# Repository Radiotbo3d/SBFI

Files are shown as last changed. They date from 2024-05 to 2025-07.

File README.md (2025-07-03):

# SBFI (Smooth Beefy Front Idlers)

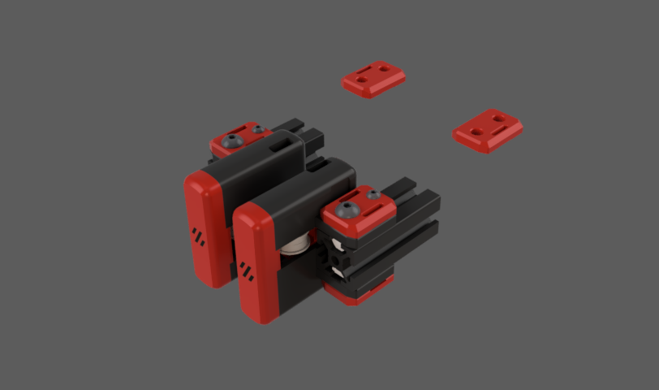
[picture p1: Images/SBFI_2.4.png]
SBFI family render

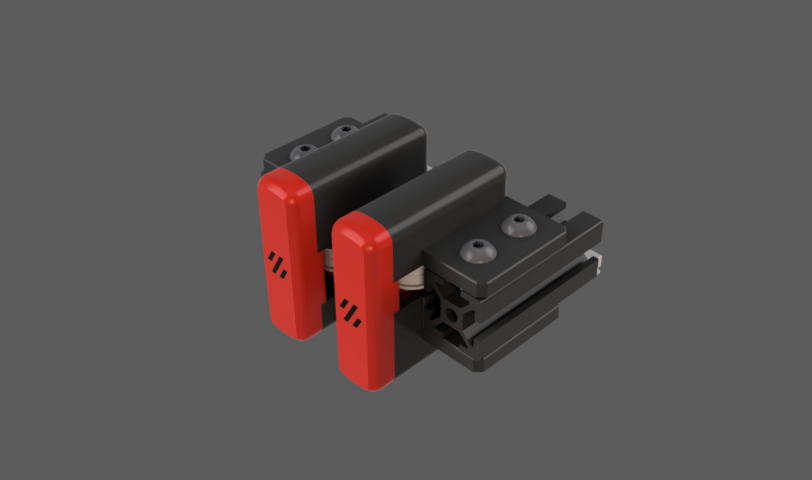
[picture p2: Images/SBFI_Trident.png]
SBFI family render


### What is this?

These are replacement front idlers for Vorons (and Voron-based machines).
This design is available for Voron Trident and Voron 2.4.

### Improvements?

This is a version remixed/based on [BFI](https://github.com/clee/VoronBFI/tree/main)
my version has several improvements or things that I have changed to fit my needs.
#### Changes:
- They are now symetrical
- They now have a magnetic cover so you don't need to see those screws anymore
- They now have curved edges instead of chamfers (very similar to [Ramalama2](https://github.com/Ramalama2/Voron-2-Mods/tree/main/Front_Idlers))

### Some more things you need to know:
You can also find this model on:
- [Clee's usermods github](https://github.com/clee/VoronBFI/tree/main/usermods#other-bfi-forksvariants)
- [Printables](https://www.printables.com/model/890840-sbfi-smooth-beefy-front-idlers)

All the clips for the z belts on the voron 2.4 are the exact same as the BFI

The internal bearing stack holder is also the exact same as the BFI (so if you had the BFI and you want to change to SBFI you don't need to reprint that part)

The front magnetic covers can be printed with MMU/AMS or you can print them as separate gcodes without removing the build plate after each print, or you can just print them with the negative of the voron logo (single color)

## BOM

### SBFI for Voron 2.4
(It's the exact same BOM as BFI but you also need 8 6x3mm magnets (4 per idler) "it will also work fine with 4 magnets (2 per idler) but I still recomend you use 8 magnets"

For V2.4, you'll need:
- 4× M5×30 BHCS 
- 4× M5 hex nuts
- 2× 5mm-diameter pin, 18mm long
- 2× M3 t-nuts
- 2× M3×16 BHCS

...plus the same shim/bearing stack setup for each idler as the original stock front idlers.

### SBFI for Trident
(It's the exact same BOM as BFI but you also need 8 6x3mm magnets (4 per idler) "it will also work fine with 4 magnets (2 per idler) but I still recomend you use 8 magnets" (and the exception that you need to change the M5x40 SHCS for M5x40 BHCS)

For Trident, you'll need:
- 4× M5×40 BHCS
- 4× M5 hex nuts
- 2× 5mm-diameter pin, 18mm long

...plus the same shim/bearing stack setup for each idler as the original stock front idlers.

## Belt / Idler Skew Tuning

BFI has a tendency to wear down belts, a known issue that occurs when the idlers are misaligned. This is also discussed in an upstream issue: https://github.com/clee/VoronBFI/issues/29.

You can use the macro below to move the tool head in a circular pattern within its range of motion. This ensures the belts keep moving consistently while you adjust the idlers.

```
[gcode_macro _TEST_BELTS]
gcode:
  {% if 'x' not in printer.toolhead.homed_axes %}
  {% if 'y' not in printer.toolhead.homed_axes %}
  G28 X Y 
  {% endif %}
  {% endif %}
 
  {% set circles = params.S|default(1)|int %}
  {% set rate = params.F|default(18000)|int %}
  {% for i in range(circles) %}
      G1 X{printer.toolhead.axis_minimum.x + 15} Y{printer.toolhead.axis_minimum.y + 15}  F{rate}
      G1 X{printer.toolhead.axis_maximum.x - 15} Y{printer.toolhead.axis_minimum.y + 15}  F{rate}
      G1 X{printer.toolhead.axis_maximum.x - 15} Y{printer.toolhead.axis_maximum.y - 15} F{rate}
      G1 X{printer.toolhead.axis_minimum.x + 15} Y{printer.toolhead.axis_maximum.y - 15}  F{rate}
      G1 X{printer.toolhead.axis_minimum.x + 15} Y{printer.toolhead.axis_minimum.y + 15}  F{rate}
    {% endfor %}
    G1 X{ printer.toolhead.axis_maximum.x / 2  } Y{printer.toolhead.axis_maximum.y  /2}  F{rate}
```

Call this macro with the parameter S to set the number of circles. For example, use `_TEST_BELTS S=20` to run 20 circles.

As the belts move, you can better observe if they are riding up on the flanges. To adjust, loosen the side you want the belt to shift toward—if it's riding up on the top flange, loosen the top bolt; if it's on the bottom flange, loosen the bottom bolt.
<br/>
<br/>
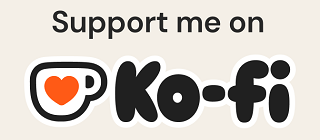
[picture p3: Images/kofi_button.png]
support me (https://ko-fi.com/radiotbo)

<br/>
## You can also support me by liking or downloading the files trough [printables](https://www.printables.com/model/890840-sbfi-smooth-beefy-front-idlers)
<br/>
# Contributors
I want to thank everyone who has helped to develop this project.

- [@clee](https://github.com/clee) (Original BFI)
- [@Ramalama2](https://github.com/Ramalama2) (Curved edges design)
- [@Shaly](https://github.com/Apstarkdev) (Improvement suggestions and testing)
- [@TheVoronModder](https://www.youtube.com/@TheVoronModder) (Improvement suggestions) (check out his [Chunky Alpaca Idlers](https://www.printables.com/model/678823-voron-24-trident-chunky-alpaca-tensioners))
- @Micky (Curved edges suggestion)
- [@Vajonam](https://github.com/vajonam) (Feedback and Macro Development)

And If someone has any suggestion for improving the design or maybe some cool features I could add, please don't hesitate to tell me.

You can either contact me through Github or through Discord "radiotbo" (I'd probably answer you faster through discord)

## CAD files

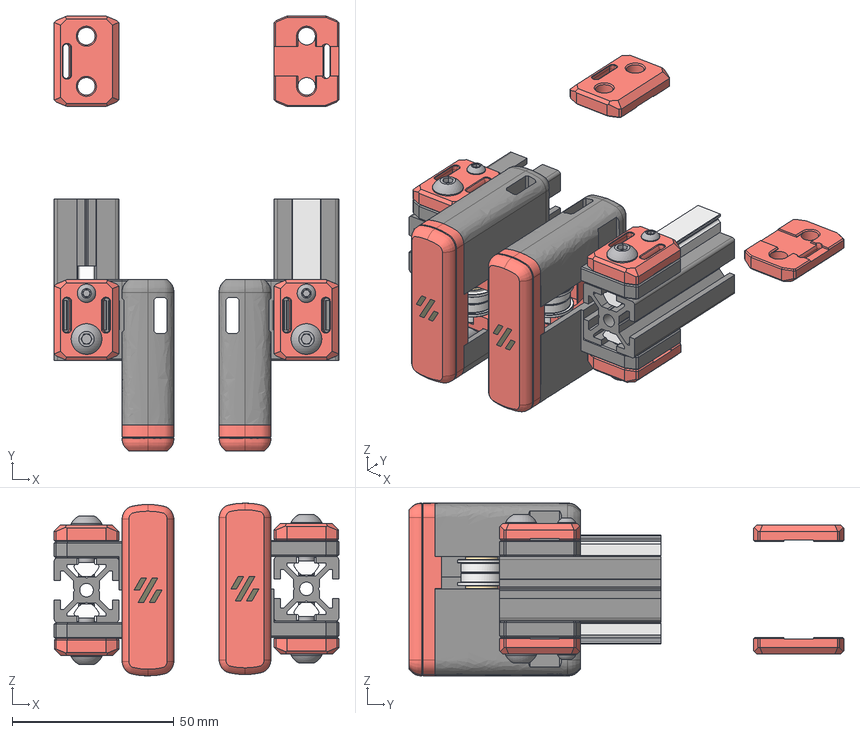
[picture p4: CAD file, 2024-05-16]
CAD/Voron_2.4/SBFI_Voron_2.4.step
88.1 x 134.5 x 53.4 mm
Printable_Parts x 2
Gantry x 2
Fasteners x 2

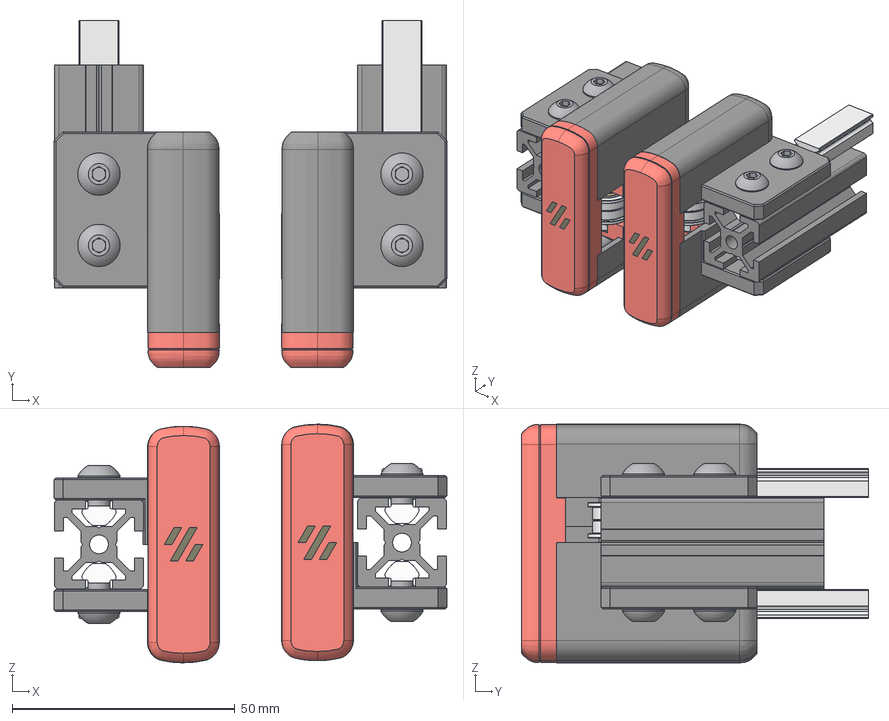
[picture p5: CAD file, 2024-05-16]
CAD/Voron_Trident/SBFI_Voron_Trident.step
88.2 x 77.9 x 53.6 mm
Printable_Parts x 2
Gantry x 2
Fasteners x 2

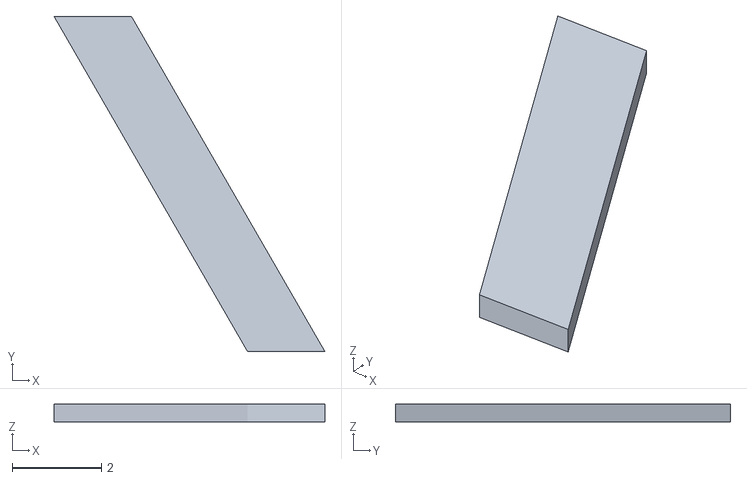
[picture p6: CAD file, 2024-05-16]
STLs/Voron_2.4/SBFI-V2.4_Voron_Logo2_x2.stl
6.06 x 7.50 x 0.4

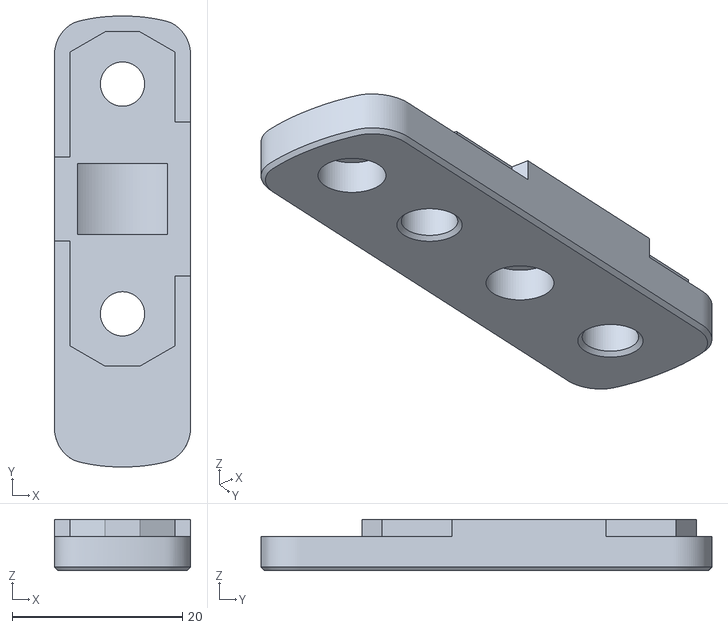
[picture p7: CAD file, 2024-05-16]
STLs/Voron_2.4/[a]_SBFI-V2.4_Middle_x2.stl
16.0 x 53.0 x 6.00

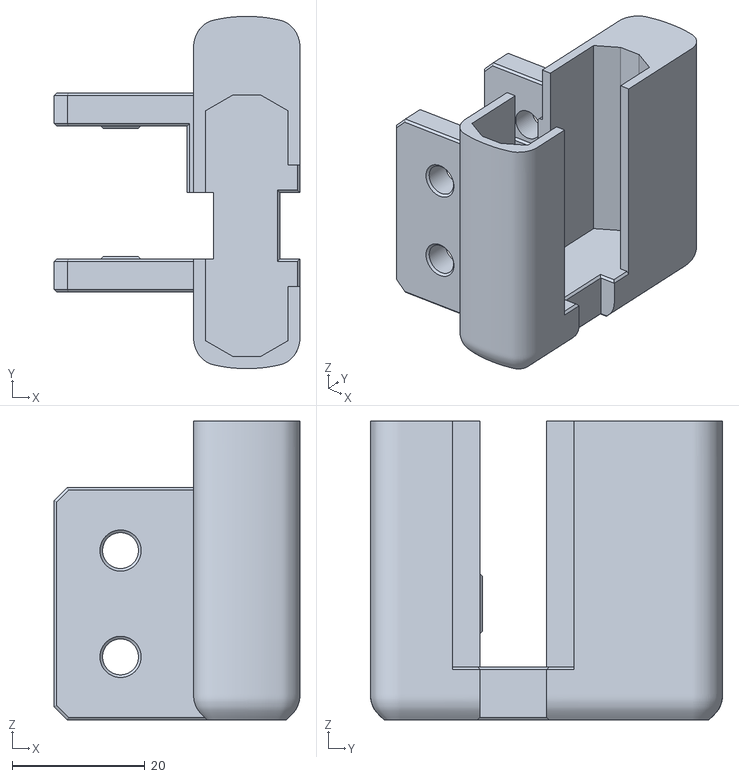
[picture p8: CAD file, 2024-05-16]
STLs/Voron_Trident/SBFI-VT_Housing_x2.stl
37.0 x 53.0 x 45.0

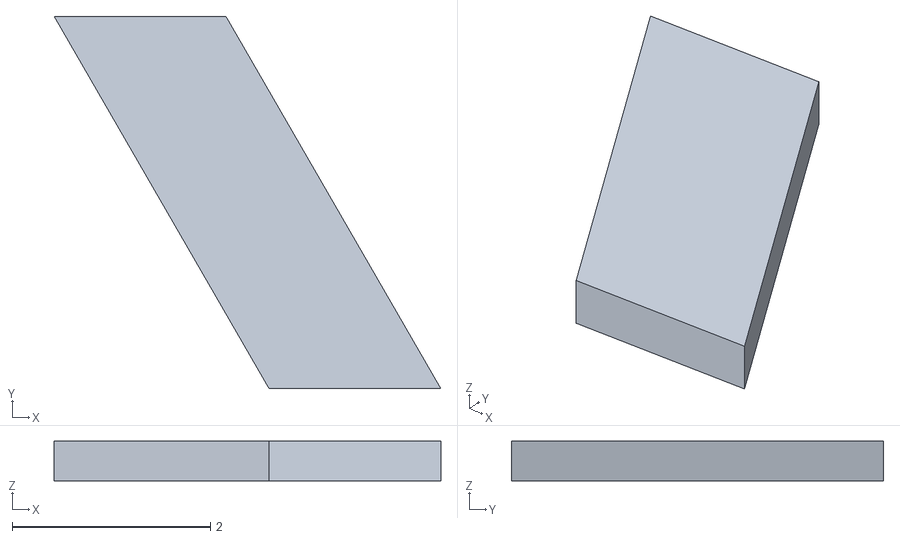
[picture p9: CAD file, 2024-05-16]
STLs/Voron_2.4/SBFI-V2.4_Voron_Logo1_x2.stl
3.90 x 3.75 x 0.4

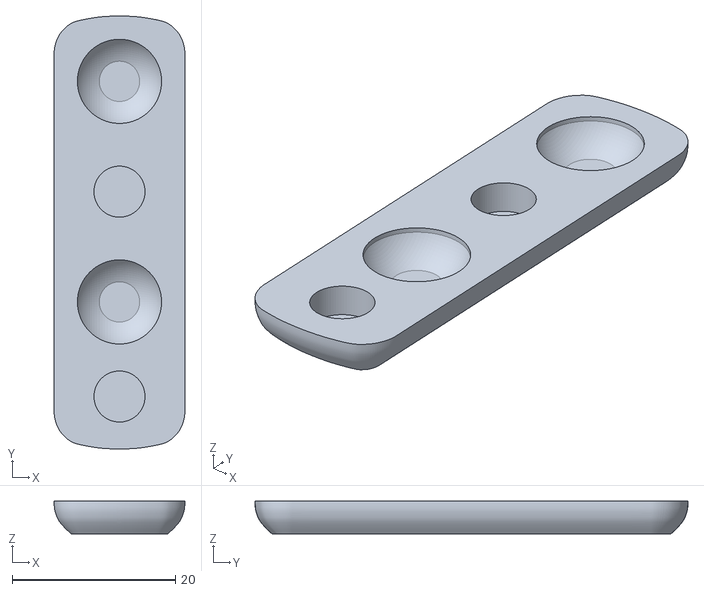
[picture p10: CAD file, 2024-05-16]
STLs/Voron_Trident/[a]_SBFI-VT_Front_Magnetic_Cover_x2.stl
16.0 x 53.0 x 4.00

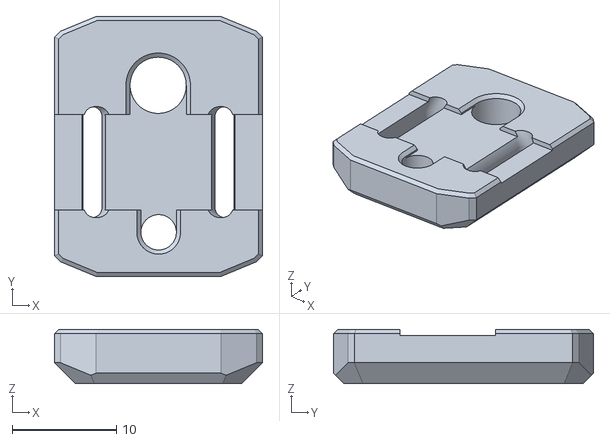
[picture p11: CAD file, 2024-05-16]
STLs/Voron_2.4/[a]_SBFI-V2.4_Belt_Clamp_x4.stl
20.0 x 25.0 x 5.20

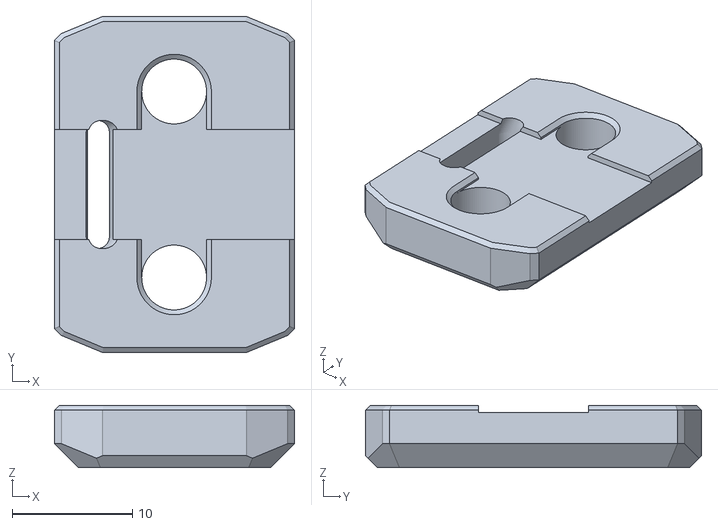
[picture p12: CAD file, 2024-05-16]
STLs/Voron_2.4/[a]_SBFI-V2.4_Belt_Clamp_AB_Drives_x2.stl
20.0 x 28.0 x 5.20

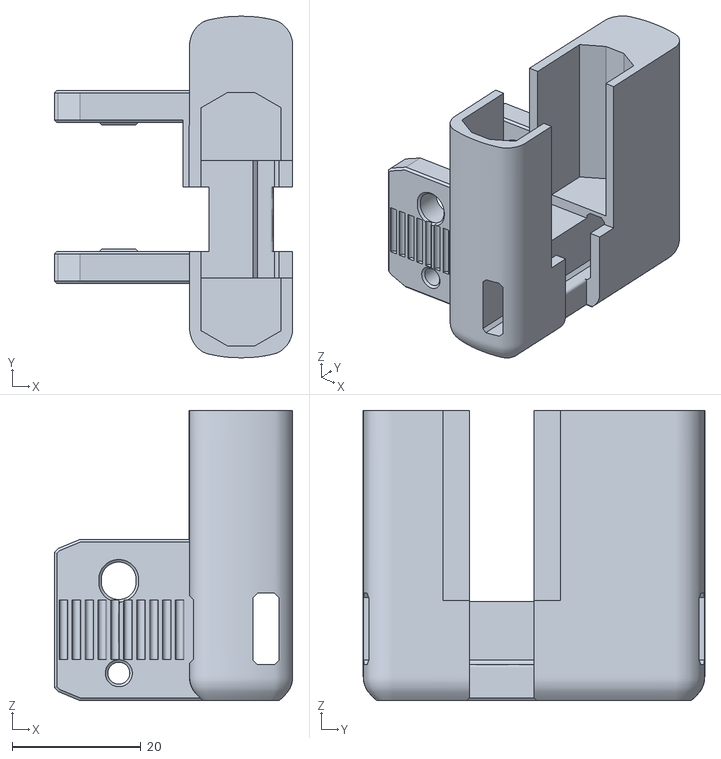
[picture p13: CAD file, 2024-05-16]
STLs/Voron_2.4/SBFI-V2.4_Housing_x2.stl
37.0 x 53.0 x 45.0

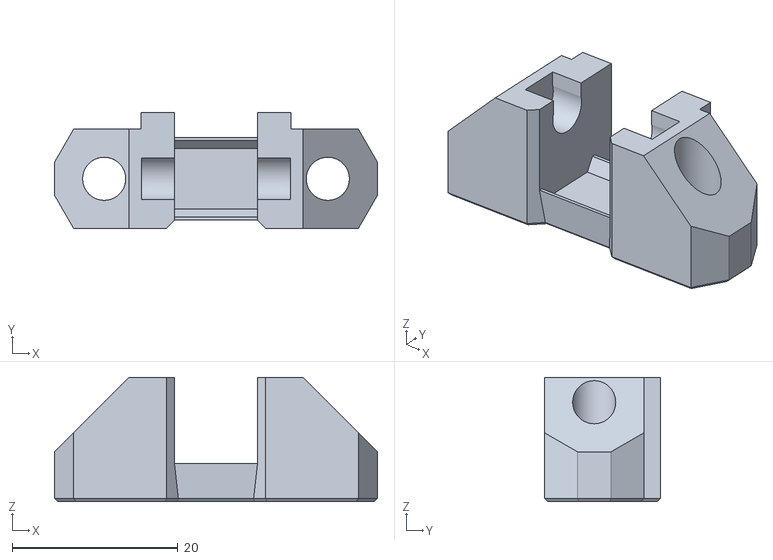
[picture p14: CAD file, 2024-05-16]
STLs/Voron_2.4/[a]_SBFI-V2.4_Carrier_x2[Use this if you want to use pins (instead of screws)].stl
39.0 x 14.0 x 15.0

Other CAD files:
STLs/Voron_Trident/SBFI-VT_Voron_Logo2_x2.stl
STLs/Voron_Trident/[a]_SBFI-VT_Middle_x2.stl
STLs/Voron_2.4/SBFI-V2.4_Voron_Logo3_x2.stl
STLs/Voron_Trident/SBFI-VT_Voron_Logo3_x2.stl
STLs/Voron_Trident/SBFI-VT_Voron_Logo1_x2.stl
STLs/Voron_2.4/[a]_SBFI-V2.4_Front_Magnetic_Cover_x2.stl
STLs/Voron_Trident/[a]_SBFI-VT_Carrier_x2[Use this if you want to use pins (instead of screws)].stl
STLs/Voron_2.4/[a]_SBFI-V2.4_Carrier_BHCS_x2[Use this if you want to use screws (instead of pins)].stl
STLs/Voron_Trident/[a]_SBFI-VT_Carrier_BHCS_x2[Use this if you want to use screws (instead of pins)].stl

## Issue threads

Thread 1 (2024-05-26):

HE instead of nut

Oasis1981, 2024-05-26:
why don't use HE instead of nut? woth ramalama works really good

Radiotbo3d, 2024-05-27:
M3 heated inserts are stronger that an M3 nut, but an M5 nut is stronger than an M5 heat insert, and also it's much more likely that you have an M5 nut rather than an M5 heat insert. I hope this answers your question. (If not let me know)

Closed 2024-07-13.

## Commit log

2024-06-11 Rename [a]_SBFI-V2.4_Carrier_x2.stl to [a]_SBFI-V2.4_Carrier_x2[Use this if you want to use pins (instead of screws)].stl
    [[a]_SBFI-V2.4_Carrier_x2[Use this if you want to use pins (instead of screws)].stl]
2024-06-11 Rename [a]_SBFI-VT_Carrier_x2.stl to [a]_SBFI-VT_Carrier_x2[Use this if you want to use pins (instead of screws)].stl
    [[a]_SBFI-VT_Carrier_x2[Use this if you want to use pins (instead of screws)].stl]
2024-06-11 Rename [a]_SBFI-VT_Carrier_BHCS_x2.stl to [a]_SBFI-VT_Carrier_BHCS_x2[Use this if you want to use screws (instead of pins)].stl
    [[a]_SBFI-VT_Carrier_BHCS_x2[Use this if you want to use screws (instead of pins)].stl]
2024-06-11 Rename [a]_SBFI-V2.4_Carrier_BHCS_x2.stl to [a]_SBFI-V2.4_Carrier_BHCS_x2[Use this if you want to use screws (instead of pins)].stl
    [[a]_SBFI-V2.4_Carrier_BHCS_x2[Use this if you want to use screws (instead of pins)].stl]
2025-02-21 Update README.md
    add idler skew tuning guide.
